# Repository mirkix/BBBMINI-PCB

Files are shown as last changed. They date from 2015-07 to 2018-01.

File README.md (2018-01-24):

# BBBMINI-PCB

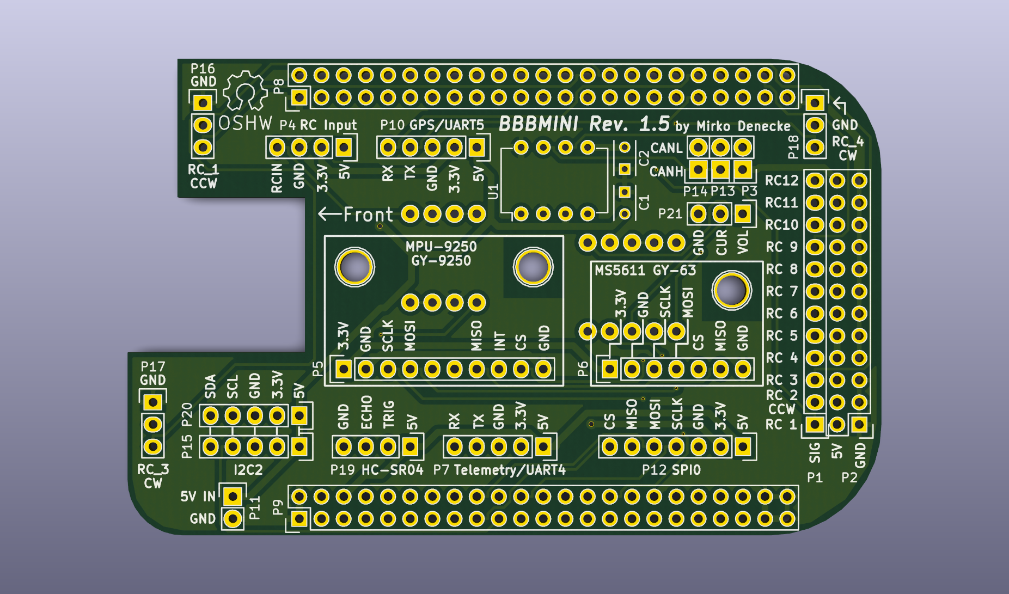
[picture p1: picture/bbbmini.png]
BBBMINI-PCB


## License

<br /><span xmlns:dct="http://purl.org/dc/terms/" property="dct:title">BBBmini</span> by <a xmlns:cc="http://creativecommons.org/ns#" href="https://github.com/mirkix" property="cc:attributionName" rel="cc:attributionURL">Mirko Denecke</a> is licensed under a <a rel="license" href="http://creativecommons.org/licenses/by-sa/4.0/">Creative Commons Attribution-ShareAlike 4.0 International License</a>.

UNLESS OTHERWISE MUTUALLY AGREED TO BY THE PARTIES IN WRITING, LICENSOR OFFERS THE WORK AS-IS AND MAKES NO REPRESENTATIONS OR WARRANTIES OF ANY KIND CONCERNING THE WORK, EXPRESS, IMPLIED, STATUTORY OR OTHERWISE, INCLUDING, WITHOUT LIMITATION, WARRANTIES OF TITLE, MERCHANTABILITY, FITNESS FOR A PARTICULAR PURPOSE, NONINFRINGEMENT, OR THE ABSENCE OF LATENT OR OTHER DEFECTS, ACCURACY, OR THE PRESENCE OF ABSENCE OF ERRORS, WHETHER OR NOT DISCOVERABLE. SOME JURISDICTIONS DO NOT ALLOW THE EXCLUSION OF IMPLIED WARRANTIES, SO SUCH EXCLUSION MAY NOT APPLY TO YOU. EXCEPT TO THE EXTENT REQUIRED BY APPLICABLE LAW, IN NO EVENT WILL LICENSOR BE LIABLE TO YOU ON ANY LEGAL THEORY FOR ANY SPECIAL, INCIDENTAL, CONSEQUENTIAL, PUNITIVE OR EXEMPLARY DAMAGES ARISING OUT OF THIS LICENSE OR THE USE OF THE WORK, EVEN IF LICENSOR HAS BEEN ADVISED OF THE POSSIBILITY OF SUCH DAMAGES.

## Changelog

Rev 1.5
* Add second I2C port
* Add current and voltage sensing
* Fix HC-SR04 voltage divider

Rev 1.4
* Add connector for Ultra Sonic Range Finder HC-SR04.
* Add 5V pin to P10 (GPS / UART4)
* Add 5V pin to P4 (RC Input)
* Add voltage divider to P4 (RC Input) pin RC_IN (RCIN) to connect 5V signals to RC_IN (RCIN)
* Add MPU-9250 interrupt singal to PRU0

Rev 1.2
* Initial commit

## BOM

### PCB

You can order BBBmini PCBs from OSHPARK https://oshpark.com/shared_projects/CtVQp1YO .

This is an example how you can get 10 BBBMINI-PCBs for less than 30$ at Shenthen2u.

Goto http://www.shenzhen2u.com/PCB 

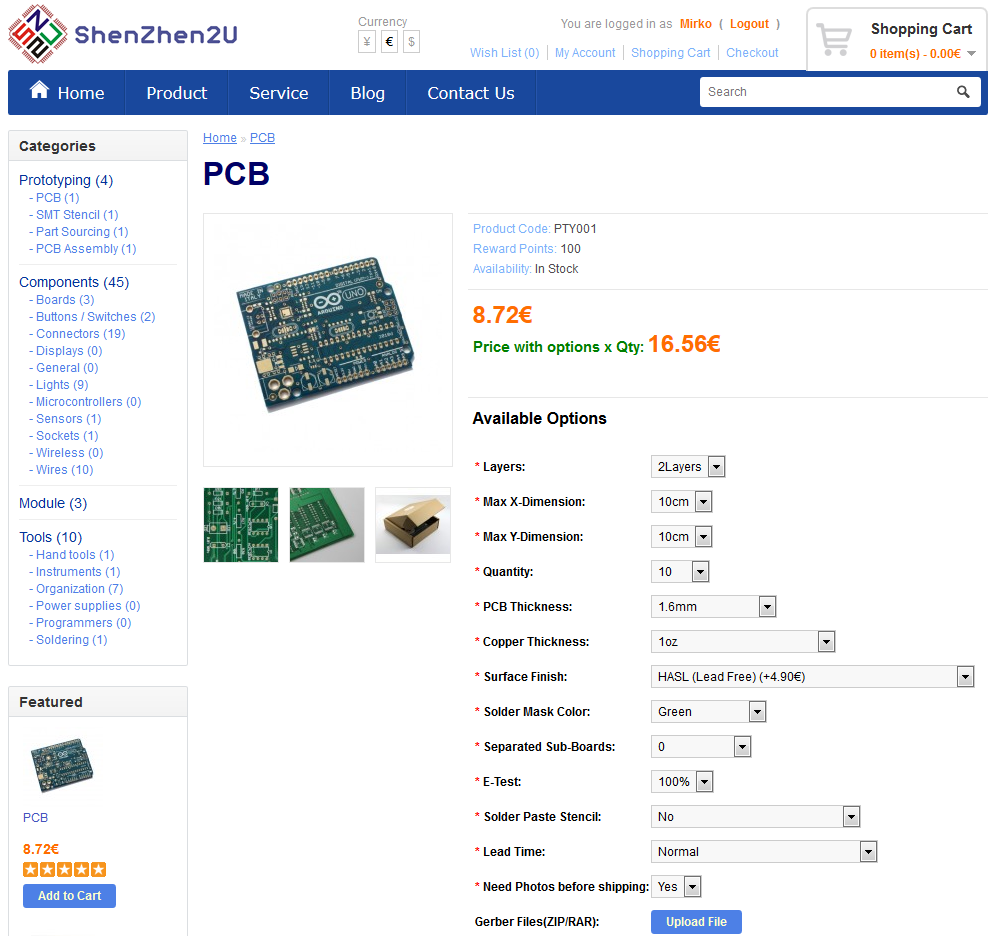
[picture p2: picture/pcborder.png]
PCB order


Upload [bbbmini.zip](kicad/gerber/bbbmini.zip) to supplier.

Finish your order.

### IMU MPU-9250

Search for GY-9250 or MPU-9250 at [aliexpress](http://www.aliexpress.com/wholesale?SearchText=gy-9250)

### Baro MS5611

Search for GY-63 or MS5611 at [aliexpress](http://www.aliexpress.com/wholesale?SearchText=gy-63)

### Rangefinder HC-SR04

Search for HC-SR04, there are a lot of sellers.

## Connector

### P1 & P2
* 2.54mm pin header 3 x 12 straight or 90°
* 12 x RC out 3.3V

### P3
* 2.54 mm pin header 1 x 2 straight
* Close this jumper to connect 5V BBBMINI power supply to P1 / P2 RC out 5V

### P4 
* 2.54 mm pin header 1 x 4 straight
* RC receiver input. 
* For 5V RCIN signal R4 = 1kOhm and R5 = 2kOhm.
* For 3.3V RCIN signal R4 = 0Ohm / bridged and R5 = open / not equipped.

### P5
* 2.54mm pin header female 1 x 10 straight
* MPU-9250 breakout board

### P6
* 2.54mm pin header female 1 x 7 straight
* MS5611 breakout board

### P7
* 2.54mm pin header 1 x 5 straight
* UART4 port
* RX and TX 3.3V signals

### P8
* 2.54mm pin header 2 x 23 straight
* BeagleBone connector, pin header has to soldered on the back of the BBBMINI-PCB

### P9
* 2.54mm pin header 2 x 23 straight
* BeagleBone connector, pin header has to soldered on the back of the BBBMINI-PCB

### P10
* 2.54mm pin header 1 x 5 straight
* UART5 port (GPS)
* RX and TX 3.3V signals

### P11
* 2.54mm pin header 1 x 2 straight
* Connector for power supply. Use this connector to power the BeagleBone Black and BBBMIN-PCB. You can also use the BeagleBone Black power plug to power the BeagleBone Black and BBBMINI-PCB.

### P12
* 2.54mm pin header 1 x 7 straight
* External SPI Bus connector for additional hardware. 
* MOSI, MISO, SCLK and CS 3.3V

### P13
* 2.54mm pin header 1 x 2 straight
* CAN Bus interface

### P14
* 2.54mm pin header 1 x 2 straight
* Close this jumper to enable 120Ohm CAN Bus resistor.

### P15
* 2.54mm pin header 1 x 5 straight
* External I2C Bus  connector for additional hardware.
* SDA and SCL 3.3V

### P16
* 2.54mm pin header 1 x 3 straight
* Additional RC_1 ESC out connector for X-Quad configuration.
* RC_1 out 3.3V

### P17
* 2.54mm pin header 1 x 3 straight
* Additional RC_3 ESC out connector for X-Quad configuration.
* RC_3 out 3.3V

### P18
* 2.54mm pin header 1 x 3 straight
* Additional RC_4 ESC out connector for X-Quad configuration.
* RC_4 out 3.3V

### P19
* 2.54mm pin header 1 x 4 straight
* Ultrasonic Range Finder connector
* Connect HC-SR04 Range Finder here.  

### P20
* 2.54mm pin header 1 x 5 straight
* External I2C Bus  connector for additional hardware.
* SDA and SCL 3.3V

### P21
* 2.54mm pin header 1 x 3 straight
* Current and voltage sensing via Power Module

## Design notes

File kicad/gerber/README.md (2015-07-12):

# Gerber Files
Content | Filename
---|---
Outline | bbbmini.GML
Drill & Holes | bbbmini.TXT
Solder Paste Top | bbbmini.GTP
Top Layer | bbbmini.GTL
Solder Paste Bottom | bbbmini.GBP
Solder Mask Top | bbbmini.GTS
Solder Mask Bottom | bbbmini.GBS
Silk Screen Top | bbbmini.GTO
Silk Screen Bottom | bbbmini.GBO
Bottom Layer | bbbmini.GBL

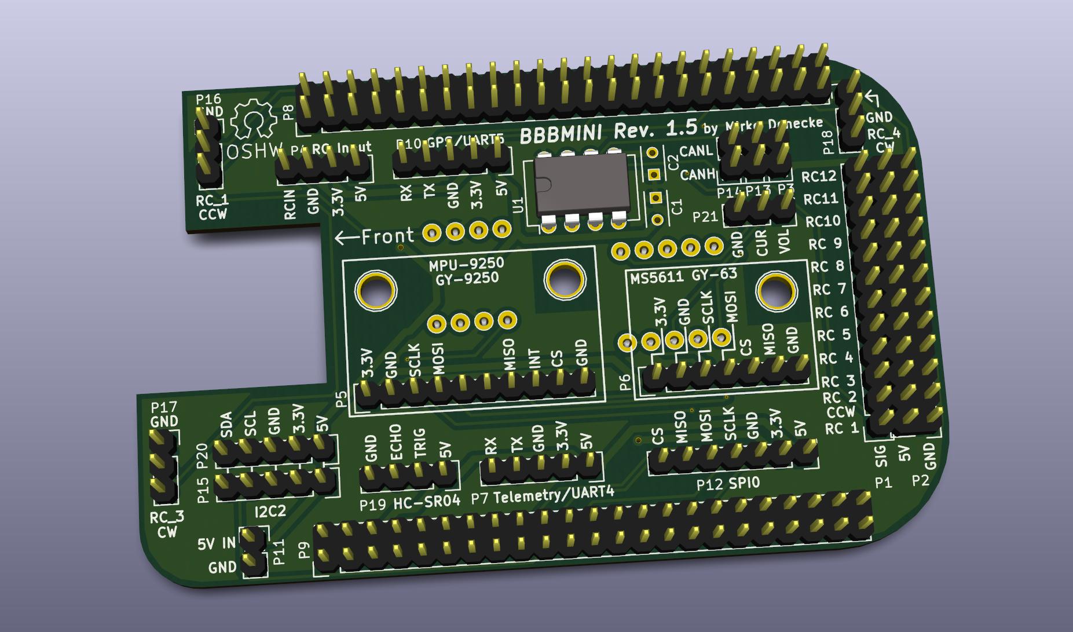
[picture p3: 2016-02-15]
picture/kicad_front.jpg

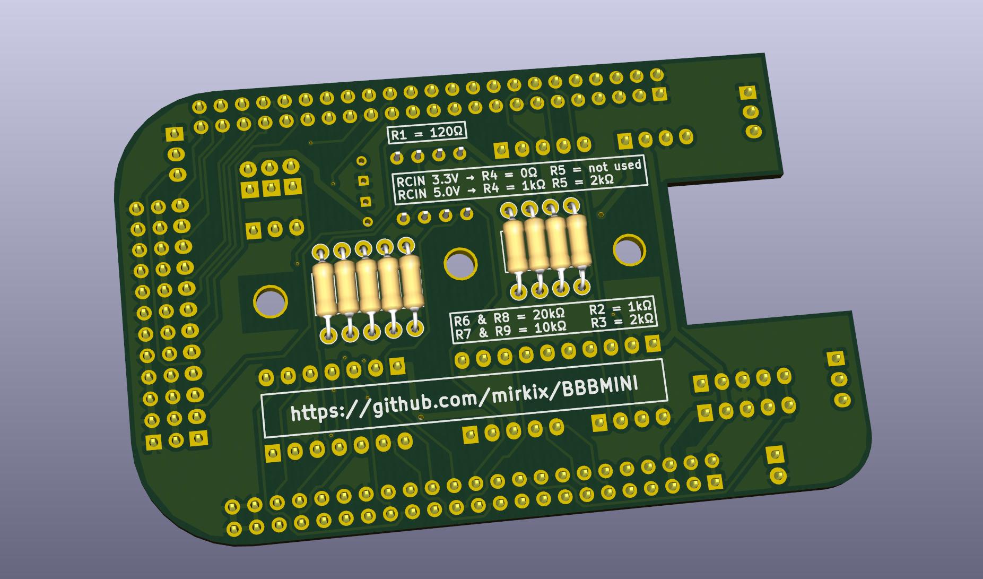
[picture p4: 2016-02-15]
picture/kicad_back.jpg

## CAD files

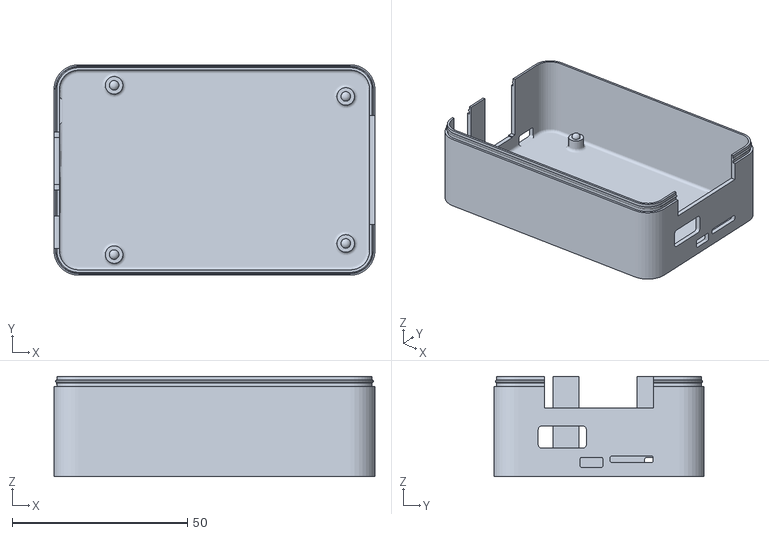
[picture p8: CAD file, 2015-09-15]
case/bbbmini_1_4_case.stl
91.5 x 60.0 x 28.5

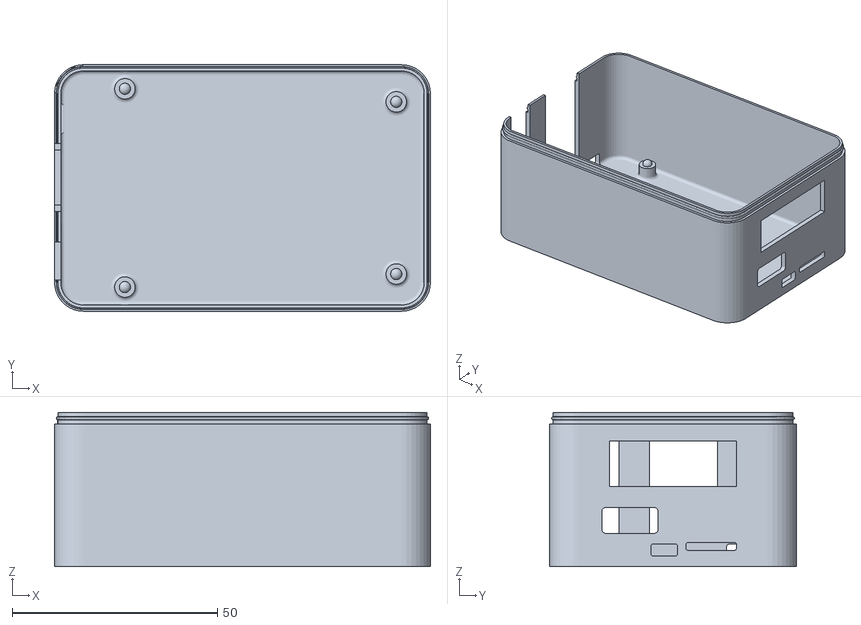
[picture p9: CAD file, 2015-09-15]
case/bbbmini_1_4_case_lifted.stl
91.5 x 60.0 x 37.5

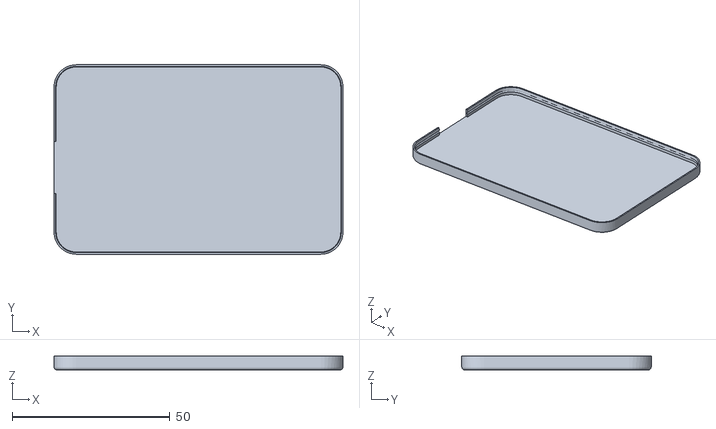
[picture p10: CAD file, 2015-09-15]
case/bbbmini_1_4_top_blank.stl
91.5 x 60.0 x 4.46

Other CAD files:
case/bbbmini_1_4_top_typo.stl

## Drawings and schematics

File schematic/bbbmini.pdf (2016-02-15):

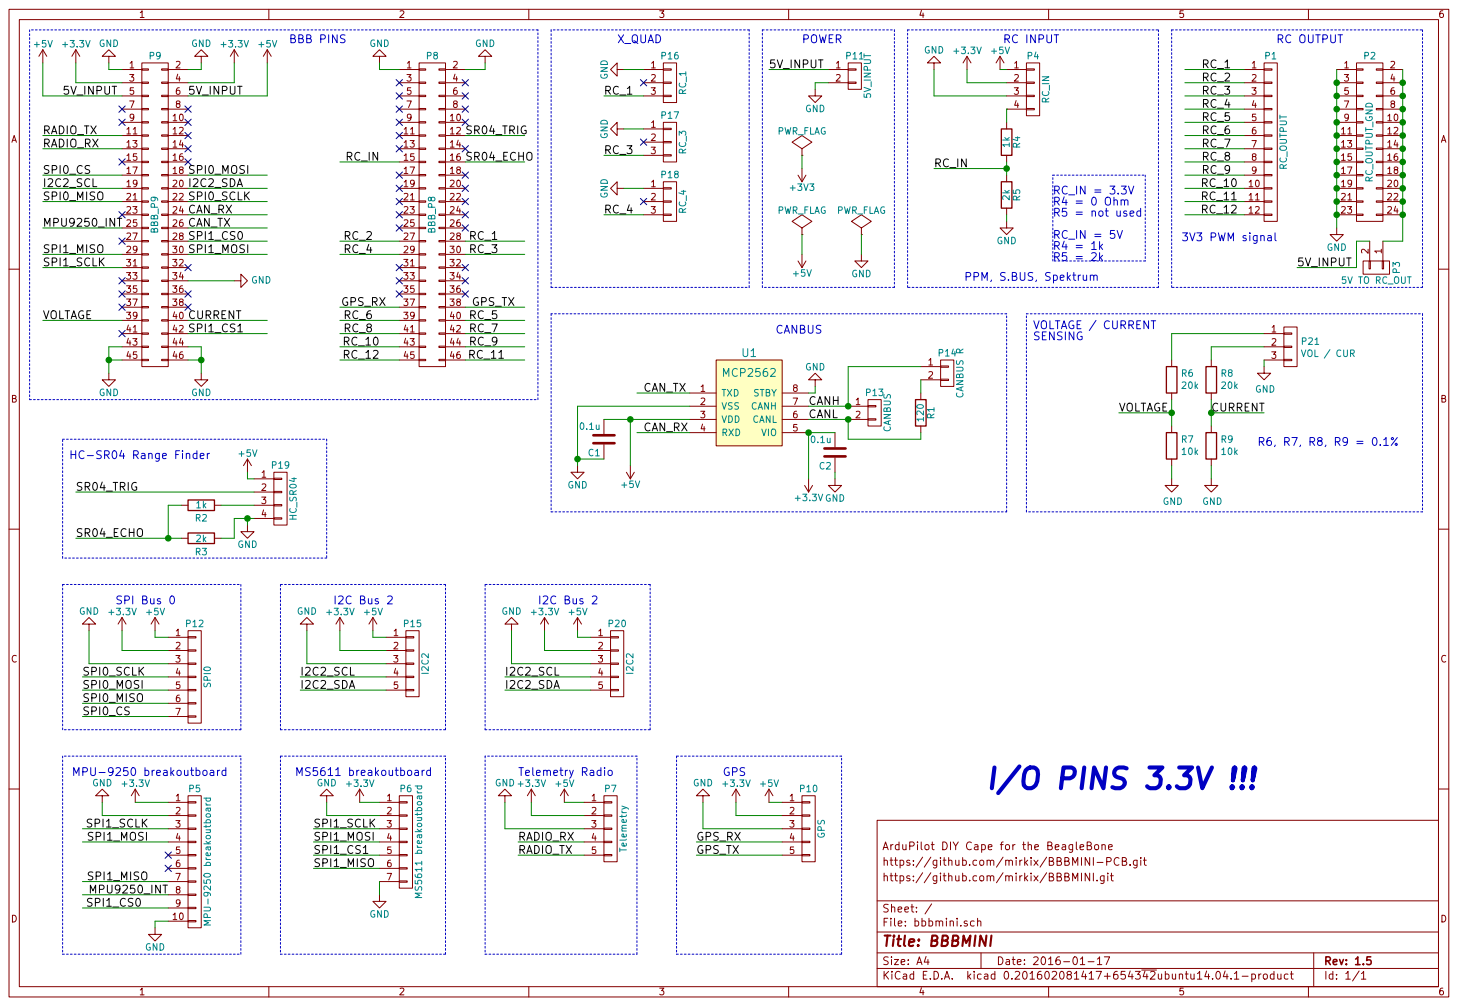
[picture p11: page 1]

CANL

CAN_RX

ArduPilot DIY Cape for the BeagleBone
https://github.com/mirkix/BBBMINI-PCB.git
Id: 1/1 Title: BBBMINI File: bbbmini.sch Sheet: / https://github.com/mirkix/BBBMINI.git

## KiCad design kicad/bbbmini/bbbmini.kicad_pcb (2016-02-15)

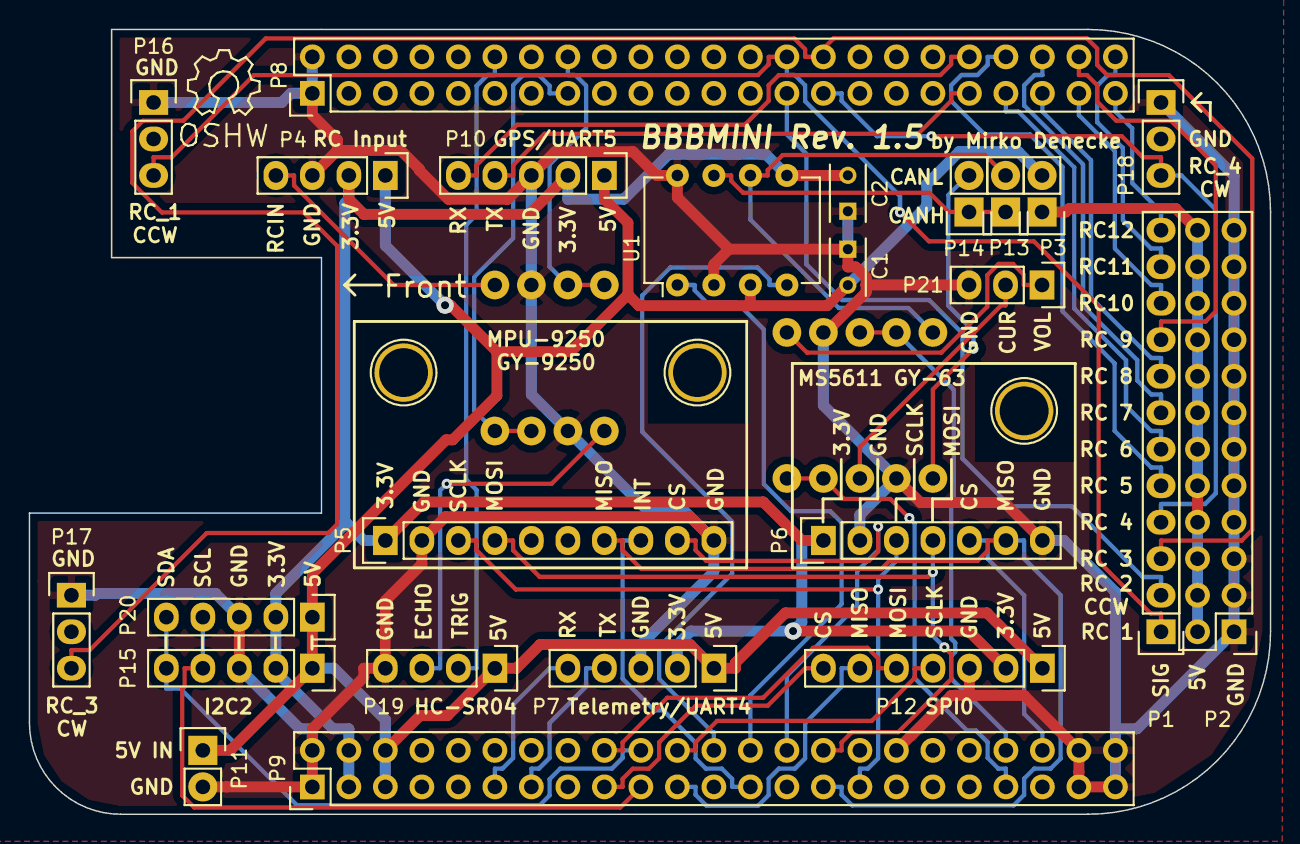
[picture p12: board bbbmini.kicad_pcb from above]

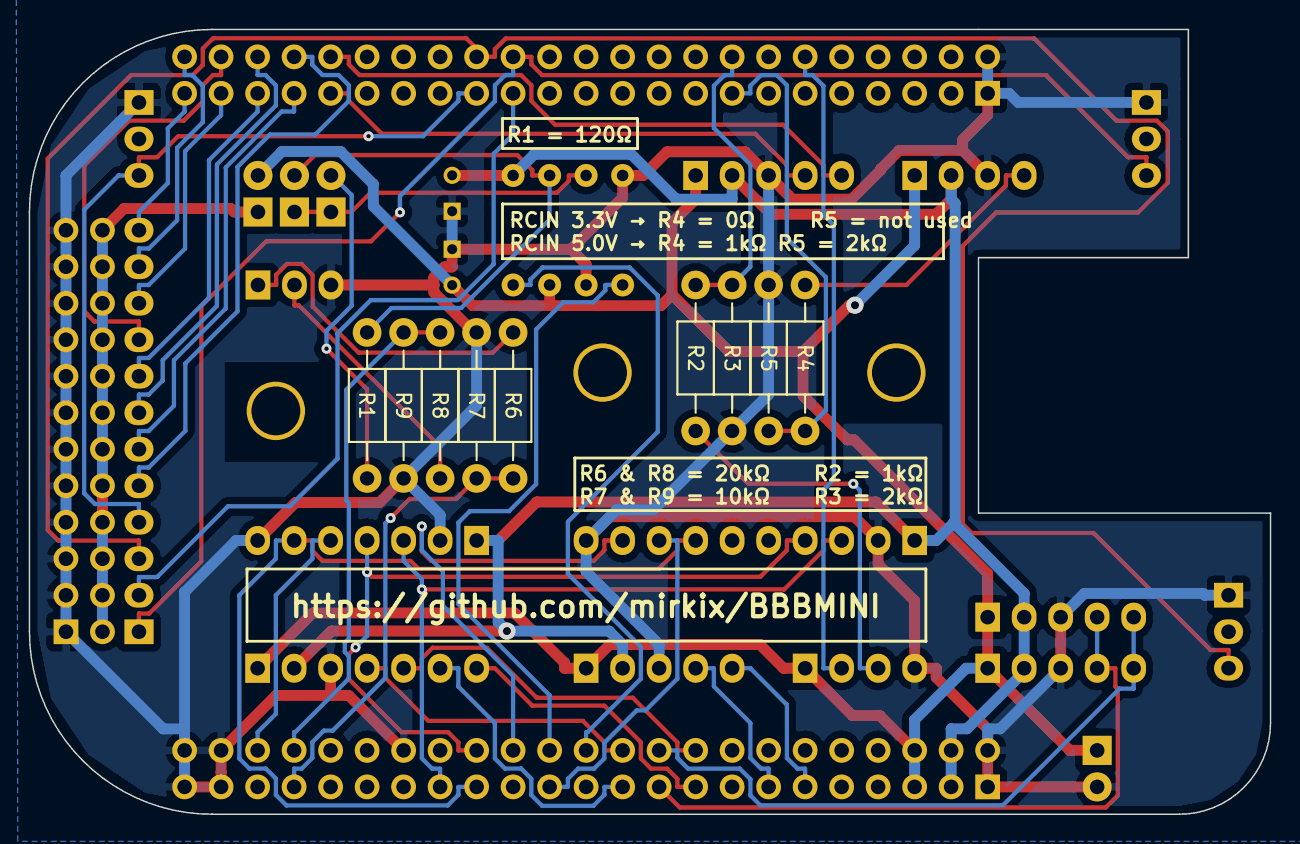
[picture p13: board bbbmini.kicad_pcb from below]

Board: 2 copper layers, 86.4 x 54.6 mm, 36 parts (9 on the bottom side), 46 nets.

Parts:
C1, C2: 0.1u; C_Rect_L4_W2.5_P2.5
P1: RC_OUTPUT; Pin_Header_Straight_1x12
P2: RC_OUTPUT_GND; Pin_Header_Straight_2x12
P3: 5V TO RC_OUT; Pin_Header_Straight_1x02
P4: RC_IN; Pin_Header_Straight_1x04
P5: MPU-9250 breakoutboard; Pin_Header_Straight_1x10
P6: MS5611 breakoutboard; Pin_Header_Straight_1x07
P7: Telemetry; Pin_Header_Straight_1x05
P8: BBB_P8; Pin_Header_Straight_2x23
P9: BBB_P9; Pin_Header_Straight_2x23
P10: GPS; Pin_Header_Straight_1x05
P11: 5V_INPUT; Pin_Header_Straight_1x02
P12: SPI0; Pin_Header_Straight_1x07
P13: CANBUS; Pin_Header_Straight_1x02
P14: CANBUS R; Pin_Header_Straight_1x02
P15, P20: I2C2; Pin_Header_Straight_1x05
P16: RC_1; Pin_Header_Straight_1x03
P17: RC_3; Pin_Header_Straight_1x03
P18: RC_4; Pin_Header_Straight_1x03
P19: HC_SR04; Pin_Header_Straight_1x04
P21: V / I; Pin_Header_Straight_1x03
R1: 120; Resistor_Horizontal_RM10mm
R2, R4: 1k; Resistor_Horizontal_RM10mm
R3, R5: 2k; Resistor_Horizontal_RM10mm
R6, R8: 20k; Resistor_Horizontal_RM10mm
R7, R9: 10k; Resistor_Horizontal_RM10mm
REF1, REF2, REF3: 1pin
U1: MCP2562; DIP-8_W7.62mm

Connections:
+3V3: C2.2, P4.2, P5.1, P6.1, P7.2, P9.3, P9.4, P10.2, P12.2, P15.2, P20.2, U1.5
+5V: C1.2, P3.2, P4.1, P7.1, P9.5, P9.6, P10.1, P11.1, P12.1, P15.1, P19.1, P20.1, U1.3
/CANH: P13.1, P14.1, U1.7
/CANL: P13.2, R1.2, U1.6
/CAN_RX: P9.24, U1.4
/CAN_TX: P9.26, U1.1
/CURRENT: P9.40, R8.2, R9.1
/GPS_RX: P8.37, P10.4
/GPS_TX: P8.38, P10.5
/I2C2_SCL: P9.19, P15.4, P20.4
/I2C2_SDA: P9.20, P15.5, P20.5
/MPU9250_INT: P5.8, P9.25
/RADIO_RX: P7.4, P9.13
/RADIO_TX: P7.5, P9.11
/RC_1: P1.1, P8.28, P16.3
/RC_2: P1.2, P8.27
/RC_3: P1.3, P8.30, P17.3
/RC_4: P1.4, P8.29, P18.3
/RC_5: P1.5, P8.40
/RC_6: P1.6, P8.39
/RC_7: P1.7, P8.42
/RC_8: P1.8, P8.41
/RC_9: P1.9, P8.44
/RC_10: P1.10, P8.43
/RC_11: P1.11, P8.46
/RC_12: P1.12, P8.45
/RC_IN: P8.15, R4.2, R5.1
/SPI0_CS: P9.17, P12.7
/SPI0_MISO: P9.21, P12.6
/SPI0_MOSI: P9.18, P12.5
/SPI0_SCLK: P9.22, P12.4
/SPI1_CS0: P5.9, P9.28
/SPI1_CS1: P6.5, P9.42
/SPI1_MISO: P5.7, P6.6, P9.29
/SPI1_MOSI: P5.4, P6.4, P9.30
/SPI1_SCLK: P5.3, P6.3, P9.31
/SR04_ECHO: P8.16, R2.2, R3.1
/SR04_TRIG: P8.12, P19.2
/VOLTAGE: P9.39, R6.2, R7.1
GND: C1.1, C2.1, P2.1, P2.3, P2.5, P2.7, P2.9, P2.11, P2.13, P2.15, P2.17, P2.19, P2.21, P2.23, P4.3, P5.2, P5.10, P6.2, P6.7, P7.3, P8.1, P8.2, P9.1, P9.2, P9.34, P9.43, P9.44, P9.45, P9.46, P10.3, P11.2, P12.3, P15.3, P16.1, P17.1, P18.1, P19.4, P20.3, P21.3, R3.2, R5.2, R7.2, R9.2, U1.2, U1.8
unnamed: P2.2, P2.4, P2.6, P2.8, P2.10, P2.12, P2.14, P2.16, P2.18, P2.20, P2.22, P2.24, P3.1
unnamed: P4.4, R4.1
unnamed: P14.2, R1.1
unnamed: P19.3, R2.1
unnamed: P21.1, R6.1
unnamed: P21.2, R8.1

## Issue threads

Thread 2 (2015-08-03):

Error opening board.

juvinski, 2015-08-03:
Hi,

I was trying to open the PBC on KiCad(build 4029 25 October 2014) on linux(Ubuntu 15.10)and receiving error:
Error loading board.
PARSE_ERROR: Unexpected 'grid_origin' in input/source "/home/juvinski/Projetos/BBBMINI-PCB/kicad/bbbmini/bbbmini.kicad_pcb", line 74, offset 6
from /build/buildd/kicad-0.20141025+bzr4029/common/dsnlexer.cpp : Unexpected() : line 317

Anyone has some clue?

Thanks

earsneyes, 2015-08-04:
@juvinski looks like you need to update your KiCad installation. Had problems opening the file as well until i upgraded KiCad.
Cheers!

juvinski, 2015-08-04:
Hi @earsneyes,

thanks for the clue. I found on Kicad website a note about it, regular Ubuntu repository use an outdated version.
Following this steps
https://code.launchpad.net/~js-reynaud/+archive/ubuntu/ppa-kicad
I could update kicad and open the diagrams

Thanks.

Regards

Closed 2015-08-04.

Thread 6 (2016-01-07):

SR04-ECHO pin level for the range finder

pierre-quelin, 2016-01-07:
Hello,
I'm not a specialist in electronic but I think there is a level problem with the SR04-ECHO input.
I think that the right schematic is a voltage divider circuit :

Echo(p19 pin3)
R2(1k)
SR04_ECHO (p8 pin15) **3.3V !!!**
R3(2k)
GND (p19 pin4)

Thank you very much for your job !

mirkix, 2016-01-07:
@pierre-quelin
Thanks! You are right (it is p8 pin16), will fix it in Rev 1.5.

Closed 2016-01-20.

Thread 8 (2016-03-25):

In the schematic both MPU9250 MS6511 are marked as using the same SPI1 bus

ashwinvasudevan, 2016-03-25:
At, https://github.com/mirkix/BBBMINI-PCB/blob/master/schematic/bbbmini.pdf
MS6511 and MPU9250, are both marked to use SPI1Bus. One of them should point to SPI0.

mirkix, 2016-03-25:
@ashwinvasudevan Both use SPI1 chip select is done via CS lines. SPI0 can be used by a second MPU-9250.

Closed 2016-03-25.

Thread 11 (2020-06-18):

Wrong assignment of resistor on CANBUS

juvinski, 2020-06-18:
Hi,

the R1 is in wrong position.
The R1 should be between CANL and CANH but instead is between the 2 outputs of CANL.
With this wrong configuration, when you up the CANBUS on linux, all the CAN network goes down.
The workaround is put a jumber on the place or R1 and insert the resistor in one CAN PAD - once they are in parallel.

pierre-quelin, 2020-12-20:
Hello,

"The termination resistors on a cable should match the nominal impedance of the cable. ISO 11898 requires a cable with a nominal impedance of 120 Ω; therefore, you should use 120 Ω resistors for termination" between CAN_L and CAN_H and not between CAN_L(P14) and CAN_L(P14).

Thank you very much for your great job.

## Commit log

2015-07-01 inital commit
    [bbbmini.GBL, bbbmini.GBO, bbbmini.GBP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]
2015-07-09 Rev 1.4
    [bbbmini.GBL, bbbmini.GBO, bbbmini.GBP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]
2015-07-11 Add BOM
2015-07-11 Add pcborder.png
2015-07-12 Add README.md for Gerber Files
2015-07-31 Add connector description.
2015-08-06 Add Rev 1.4 BOM
2015-09-15 Move case from BBBMINI to BBBMINI-PCB
    [bbbmini_1_4_case.stl, bbbmini_1_4_case_lifted.stl, bbbmini_1_4_top_blank.stl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]
2016-01-03 add kicad 3d view screenshots
2016-02-15 Rev. 1.5
    [bbbmini.GBL, bbbmini.GBO, bbbmini.GBP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]
2016-02-17 Updated BOM for 1.5 rev
    Added resistors for the new rev 1.5 boards
